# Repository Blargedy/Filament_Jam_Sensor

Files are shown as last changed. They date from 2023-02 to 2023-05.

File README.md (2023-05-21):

# Tasty-Sensor
A sensor that detects jams made of organic home-grown filament, and also runout.





The Tasty-Sensor detects if the filament gets stuck on the way to the nozzle, or if the filament ran out but didn't get jammed like it usually does.

I needed a sensor that detects when the filament runs out, but I couldn't find one that worked for me, so I designed my own. A regular runout sensor sometimes worked if the hook at the end of a spool was gentle enough to slip through the sensor, but almost always the filament got stuck on the end of the sensor and the print failed silently. Sensors that check for filament movement (such as the BTT Smart Filament Sensor) gave me too many false positives even after the recommended tuning and adjustment. The sensor that got the closest to what I wanted is the SpEye by MirageC [thingiverse](https://www.thingiverse.com/thing:4299458) | [docs.hevort](http://docs.hevort.com/#/pages/Mods/spy-eye.md)

The SpEye introduced too much friction in the filament path to be feasible to me. The primary cause for this was the plunger binding and the filament sliding along the bearings instead of letting the bearings roll. The binding of the plunger comes from a direct plastic-to-plastic movement interface, and the spring tension acting offset from the center of rotation, causing a moment in the plunger. The SpEye needs two different stiffnesses of springs to function properly, and I didn't have two springs the right length and with different enough stiffness.

I sought to solve these issues in my design. The features of the Tasty-Sensor are as follows:

* Spring tension is aligned with the center of mass
* Only a single spring is needed 
* Plunger runs on bearings to reduce friction
* TPU tires on bearings let the bearings roll instead of having the filament slide over them

The primary drawbacks of this design are:

* Needs 6 bearings instead of 3
* Needs more parts printed
* Needs more fasteners
* Spring tension cannot be tuned and needs a spring swap for switching from ABS to flexible for example
* Loading filament is slightly harder







## BoM
* 2pcs M3x8 BHCS
* 5pcs M3x10 SHCS
* 2pcs M3x12 SHCS
* 2pcs M3x25 SHCS
* 6pcs M3 hex nuts
* 2pcs M3 5mmWx4mmH threaded heat inserts
* 2pcs PC4-M6 pneumatic fittings
* 1pcs Optical Sensor
* 6pcs 623zz bearings
* 6pcs 5mmOD 3mmID 0.5mmH Shims

## Printing Recommendations

* Print the filament guides in 0.1mm layer height.
* Print everything else in 0.2mm layer height.
* Clearances were calibrated for eSun ABS+ and Polymaker ASA. Polymaker ABS could be used but it shrinks slightly more so fitment is tighter. Other filaments are untested.
* Clearances are sensitive to EM innacuracies and elephants foot so make sure you've tuned those properly.

## Instructions
1. Melt on the heat inserts




2. Insert hex nuts, pulling them tight with an M3 bolt



3. Press fit the filament guides onto three bearings


4. Attach the bearing to the tensioner with an M3x8 BHCS


5. Insert the tensioner into the tensioner pocket


6. Attach the bearing with the middle filament guide onto plunger with an M3x8 BHCS


7. Place the plunger onto the vertical channel, then move the tensioner loosely into position


8. Attach the rest of the bearings with M3x10 SHCS


9. Gently push the tensioner into the plunger with your finger, then loosely tighten the set screw so that the tensioner won't back off but not so much that the plunger binds. You must maintain smooth movement. 


10. Insert the spring into the plunger cutout and test to see if you still have full range of motion on the plunger. It must be able to move the same amount with the spring in as without the spring. 


11. Install the optical sensor with M3x12 SHCS


12. Screw on the Pneumatic tube fitments directly into the plastic 


13. (Optional) Attach the tasty-sensor to your printer frame with the standoffs and M3x25 SHCS


14. Connect 5v, Signal, and Ground to the optical endstop

15. Add the following to your printer.cfg file:
```
[filament_switch_sensor filament_sensor]
switch_pin: !<your pin>
pause_on_runout: True
insert_gcode:
    M117 Insert Detected
runout_gcode:
    M117 Runout Detected

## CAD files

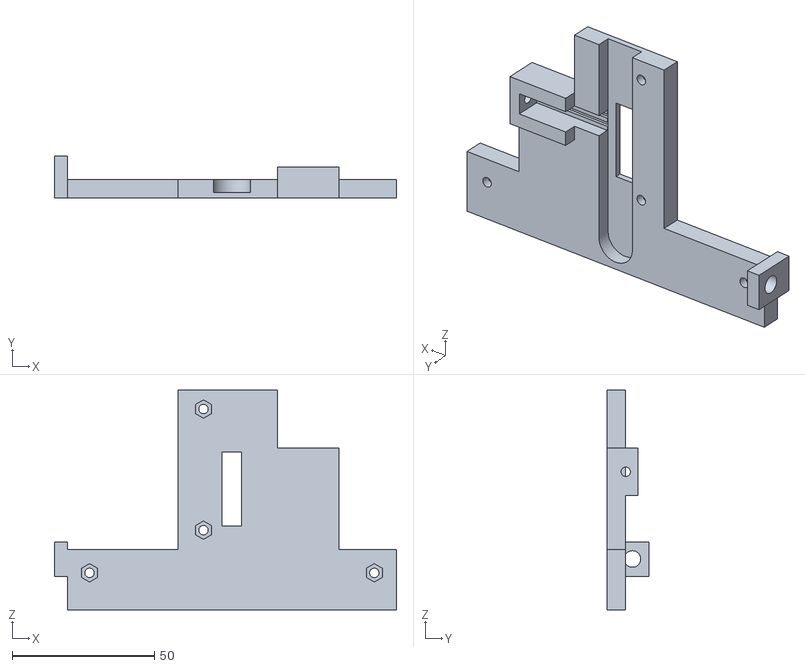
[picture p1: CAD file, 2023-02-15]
STLs/main_body.stl
120.1 x 14.9 x 77.2

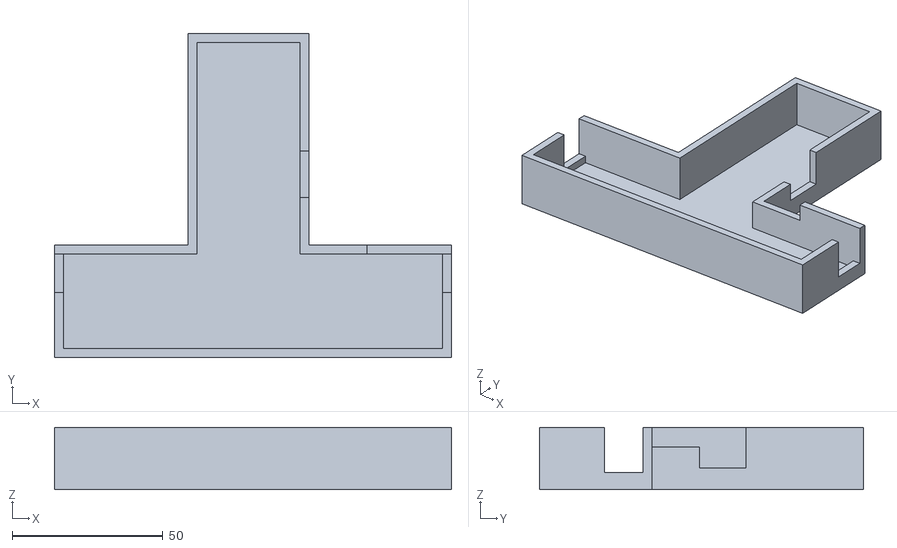
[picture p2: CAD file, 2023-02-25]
STLs/Lid.stl
131.9 x 107.7 x 20.7

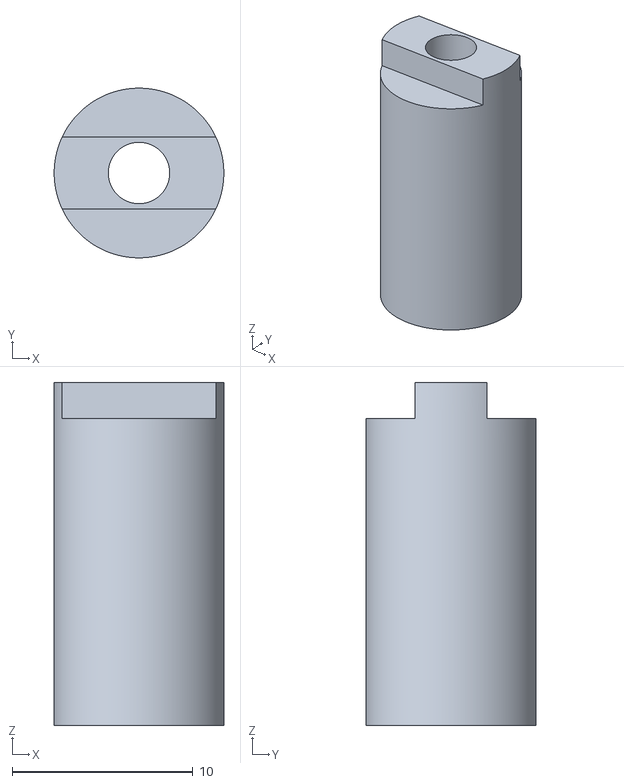
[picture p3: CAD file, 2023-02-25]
STLs/2020_rail_mount_standoff_x2.stl
9.40 x 9.40 x 19.0

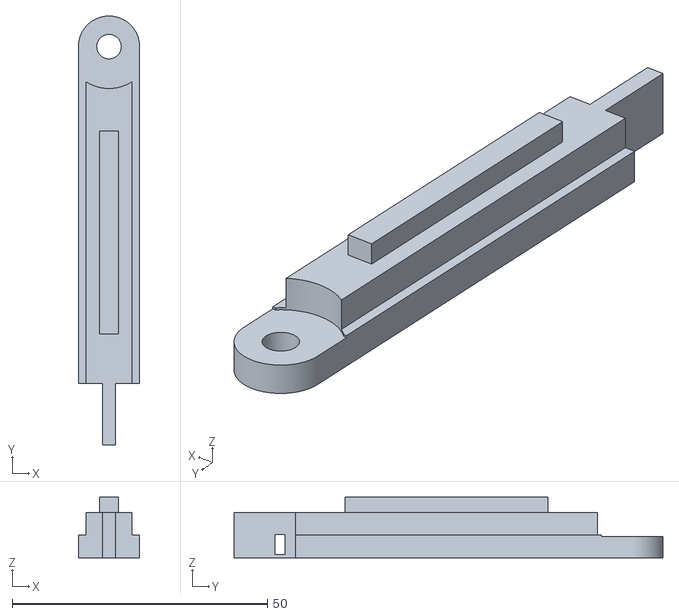
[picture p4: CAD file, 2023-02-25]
STLs/Plunger_B.stl
12.0 x 84.0 x 11.9

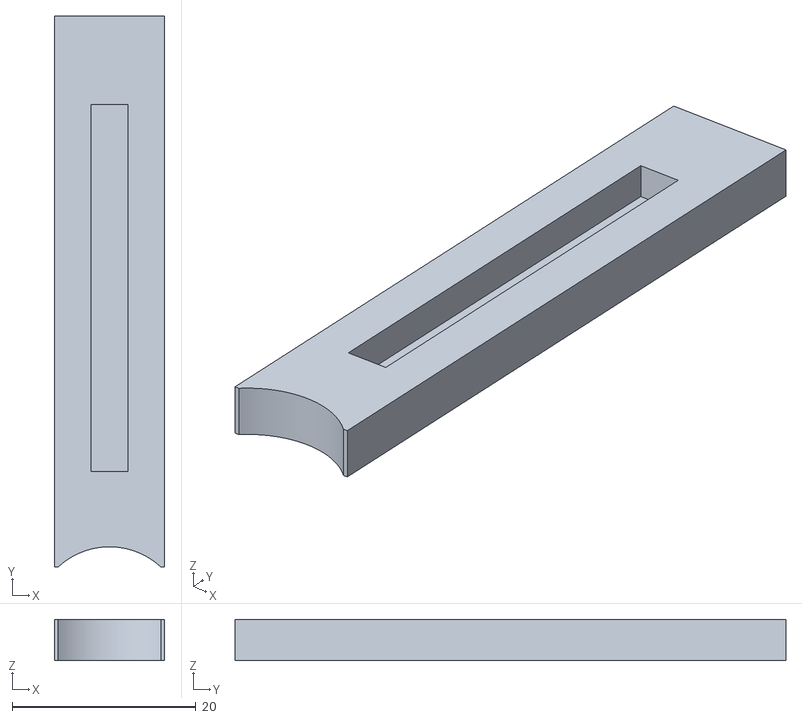
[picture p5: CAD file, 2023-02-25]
STLs/Plunger_A.stl
12.0 x 60.0 x 4.50

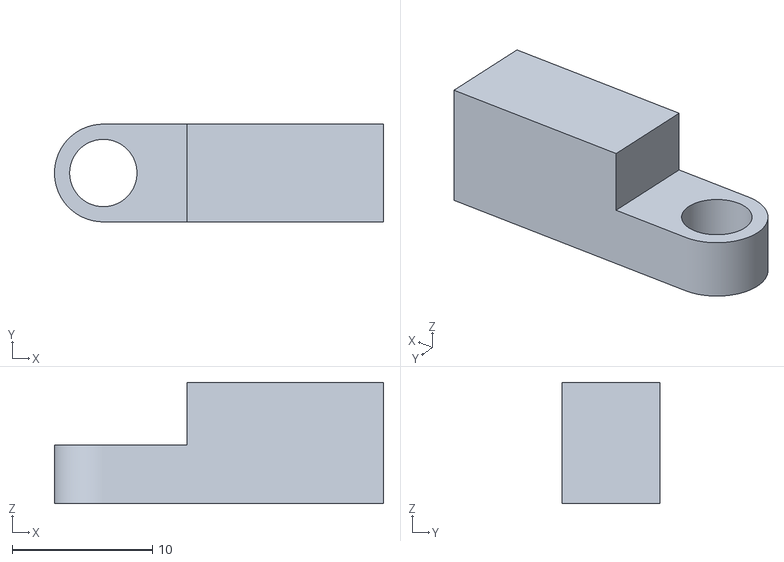
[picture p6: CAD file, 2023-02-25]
STLs/tensioner.stl
23.5 x 6.97 x 8.66

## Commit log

2023-02-15 first test pieces
    [main_body.stl, plunger.stl, spring_block.stl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]
2023-02-15 made main body printable
    [main_body.stl, plunger.stl]
2023-02-21 first version
    [Lid.stl, Plunger_A.stl, Plunger_B.stl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]
2023-02-22 lengthened runout tab since it didn't reach sensor
    [Plunger_A.stl, Plunger_B.stl]
2023-02-22 renamed filament guides as flex clearances are different
    [spring_block.stl]
2023-02-25 switch to single sensor
    [Plunger_B.stl]
2023-02-25 Fix orientation. Add standoffs.
    [2020_rail_mount_standoff_x2.stl, Lid.stl, Plunger_A.stl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]
2023-02-25 fix plunger clearance
    [Lid.stl]
2023-06-05 removed need for filament guides
